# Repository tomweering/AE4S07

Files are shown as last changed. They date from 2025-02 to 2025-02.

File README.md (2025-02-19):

# AE4S07: Micropropulsion Individual Project 

## Project ID: 60d Parallelepiped Tank Design for CubeSat  
**Supervisor:** A. Cervone  
**Type:** Analysis + Design  

## Overview
Designing a parallelepiped-shaped tank for a green mono-propellant CubeSat system, using additive manufacturing techniques.

## Model Render

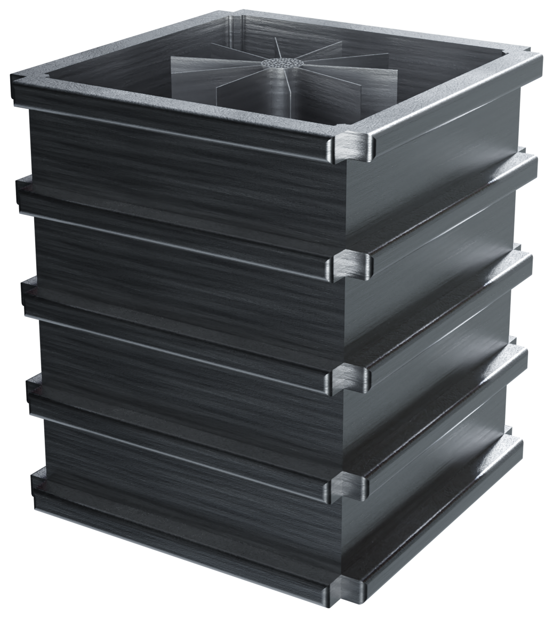
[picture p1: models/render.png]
Parallelepiped Tank Render


## Keywords
CubeSat, Propulsion, Parallelepiped Tank, Green Propellant, Additive Manufacturing

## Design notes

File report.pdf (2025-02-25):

AE4S07 Micropropulsion: Individual Project TU Delft
February 2025
Tom Weering

Tom Weering 5009057

## Report 60d Preliminary design of a parallelepiped-shaped tank for CubeSat green mono-propellant systems

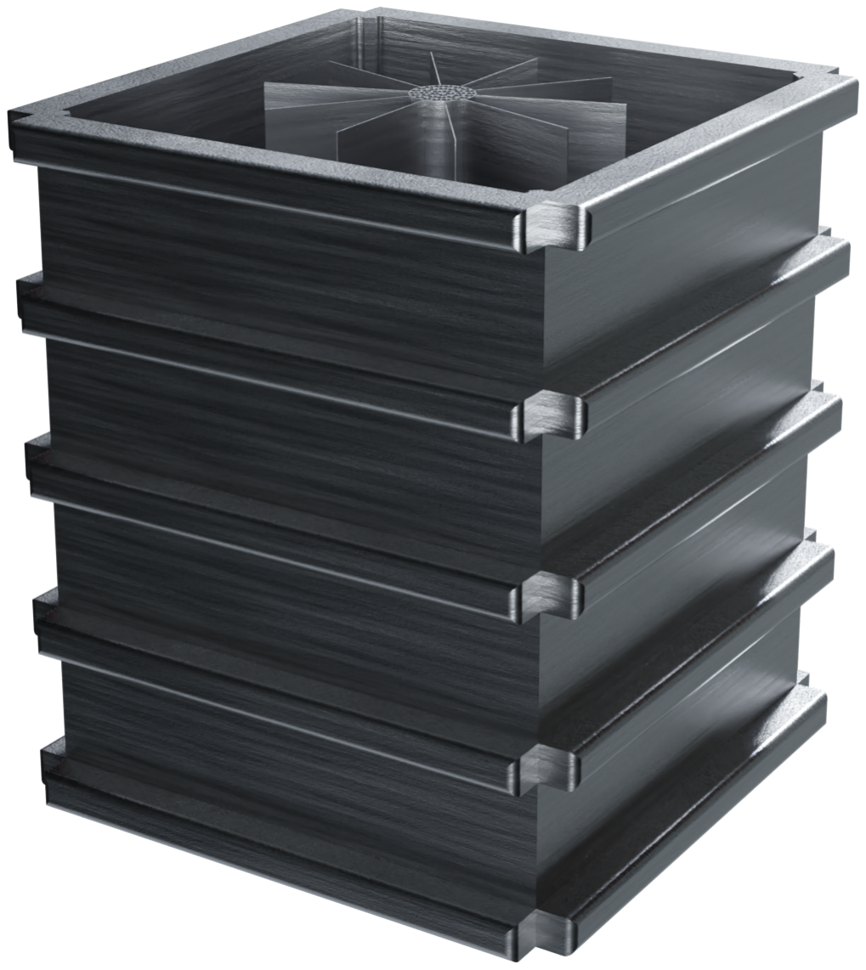
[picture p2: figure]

## Problem Formulation

As space miniaturization advances, it becomes increasingly important to integrate diverse fields of knowledge, such as green fuels, advanced manufacturing techniques, and innovative design shapes, to drive progress in the sector. This project focuses on the analysis and preliminary design of a CubeSat propellant tank with a parallelepiped shape, utilizing additive manufacturing (AM) techniques for green monopropellants. The goal is to design a competitive design solution, taking note of their respective advantages and disadvantages (Table 1).

Designing a parallelepiped-shaped propellant tank for CubeSats introduces both challenges and opportunities, especially when incorporating AM techniques and green monopropellants. The parallelepiped geometry offers space efficiency and modularity, which

Individual Project | Tom Weering

simplifies spacecraft integration. However by it’s nature it is not an ideal shape for a pressure vessel which will limit the internal pressure.

AM also presents multiple benefits for CubeSat propulsion systems, including rapid prototyping and simplyfing the manufacturing process. It also enables the creation of more complex geometries. AM also supports high-performance alloys, such as Ti-6Al-4V and Inconel [14], ensuring structural integrity and chemical compatibility with green monopropellants. Nevertheless, challenges remain, such as post-processing requirements for flight-grade standards, print orientation, thermal issues, the need for supports etc.

Green monopropellants offer improved safety, lower toxicity, reduced environmental impact, and competitive performance compared to traditional propellants. Additionally, they exhibit better storage stability. However, due to their relatively recent development and limited testing, it is important to consider their compatibility with the selected structural material, propulsion management systems, and other related components.

Advantages | Disadvantages
Parallelepiped-Shaped Tanks
Space Efficiency | Sharp corners
Modularity | Pressure limited
| Additive Manufacturing
Rapid Prototyping | Surface Finish
Complex Geometries | Chemical Compatibility
Green (Mono-)Propellant
Safety | Chemical Compatability
Storage Stability | Limited Knowledge

Table 1: Key Advantages and Disadvantages of Parallelepiped-Shaped Tanks, Additive Manufacturing, and Green Monopropellants.

The success of this project hinges on a comprehensive understanding of the interaction between these factors, with the goal of designing a propellant tank that aligns with our current knowledge of these interactions. The design will aim to provide a solution that is easily integrable into existing CubeSat formats (primarily 3U, as detailed later) and leverages the capabilities of current additive manufacturing (AM) techniques, ensuring compatibility with green monopropellants. In doing so this report aspires to answer the following two research questions:

RQ1: What is the most suitable design for a parallelepiped-shaped tank, to meet the identified constraints and requirements?

RQ2: What are the most suitable materials, dimensions and shape/fluidic interfaces which allow for a fully operational design of the tank?

## Requirements

Before exploring potential design options and developing a preliminary design, it is essential to first define the problem through a set of requirements. This was achieved through an internal literature review, including an analysis of the Lunar Flashlight mission [12], reference to design manuals for pressure vessels [4], and research into constraints associated with additive manufacturing [1] and the use of green monopropellants [15]. Following a systems engineering approach, top-level requirements were established and subsequently broken down into related sub-requirements, resulting in the requirements discovery tree illustrated in Figure 1.

The requirements highlighted in light green represent stakeholder requirements, derived directly from the project description. Below these are system-level requirements, followed by more specific requirements that pertain to "subsystems" of the tank being designed. These subsystems include structural aspects, propellant management devices, CubeSat design specifications, and constraints related to additive manufacturing.

Each requirement is assigned a unique ID in the format PAMGMT-STK-XX-SYS-SUB-XX, where SUB represents one of the four subsystems: STR (Structure), PMD (Propellant Management Device), CDS (CubeSat Design Specification), or AM (Additive Manufacturing). The acronym PAMGMT stands for Parallelepiped-shaped Additively Manufactured Green Monopropellant Tank. This structured approach ensures clear traceability, linking each requirement to higher-level system goals and demonstrating how individual requirements contribute to fulfilling broader, less strictly defined objectives. The complete overview listing every requirement along with the associate rationale for including them is given in the Table below (see Table 3).

An implicit requirement is that the selected material must be compatible with L-PBF or EB-PBF additive manufacturing processes and chemically resistant to green monopropellants. According to literature [14], several materials have been identified as suitable for these manufacturing techniques, with some also exhibiting favorable chemical compatibility with green monopropellants. Table 2 provides an overview of these materials. These options will serve as the foundation for material selection in the subsequent preliminary design phase. In the table, "A" indicates excellent chemical compatibility with the specified green monopropellant. Throughout this report, L-PBF will be used as the default method for additive manufacturing, as EB-PBF generally involves higher costs due to the requirement for a vacuum environment [7]. However, if thermal issues arise with L-PBF, EB-PBF may be considered as an alternative (except for SS304L).

Table 2: Material Compatibility with Green Propellants [14]

MATERIAL | HNP225 | LMP103S | AFM315E | FLP-106
Ti-6Al-4V | A | A | A | A
SS316L | A | A | A | A
SS304L | A | A | A | A
Inconel 625 | A | A | A | A

*Only compatible with L-PBF (Laser Powder Bed Fusion) process.

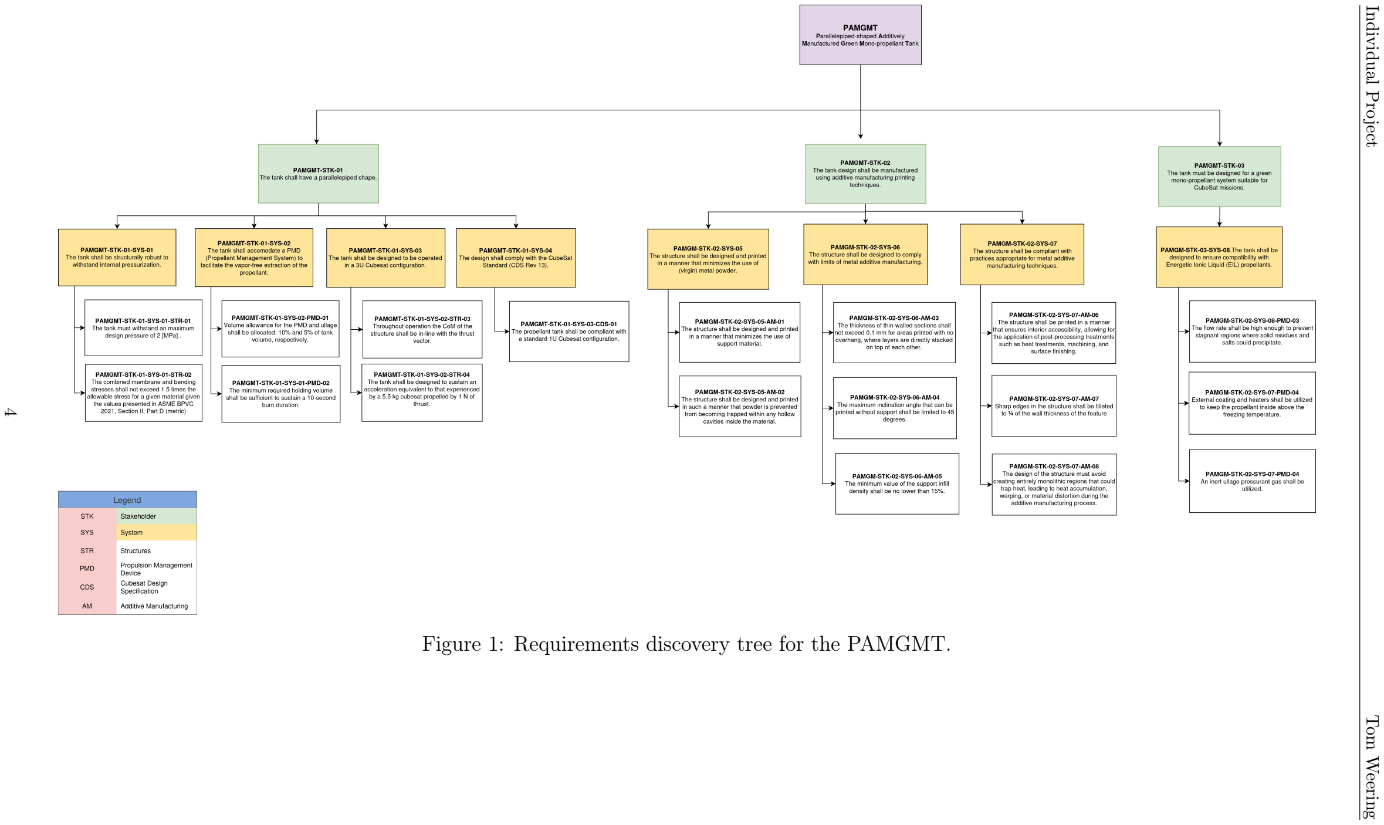
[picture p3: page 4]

Individual Project Tom Weering Figure 1: Requirements discovery tree for the PAMGMT.

4

Individual Project Tom Weering Requirement Index Description Rationale PAMGMT-STK-01 The tank shall have a parallelepiped shape. Defined by supervisor. PAMGMT-STK-01-SYS-01 The tank shall be structurally robust to withstand internal pressurization. Regardless of the PMD, engine type, or propellant used, some ullage pressure is necessary. Given the tank’s parallelepiped shape, special attention must be paid to ensuring structural integrity. PAMGMT-STK-01-SYS-01-STR-01 The tank must withstand an maximum design pressure of 2 [MPa]. monopropellant microthrusters produce 0.1–1 N of thrust [6], and for a specific 1 N thruster, chamber pressure ranges from 0.45 to 2.2 MPa [15]. To accommodate various thruster types, a Maximum Design Pressure (MDP) of approximately 2 MPa was chosen. PAMGMT-STK-01-SYS-01-STR-02 The combined membrane and bending stresses shall not exceed 1.5 times the allowable stress for a given material given the values presented in ASME BPVC 2021, Section II, Part D (metric) The sizing must go according to standardization practices appropriate for pressure vessels. The ASME (The American Society of Mechanical Engineers) sizing for infinite rectangular pressure vessels was adapted for this purpose. PAMGMT-STK-01-SYS-02 The tank shall accomodate a PMD (Propellant Management System) to facilitate the vapor-free extraction of the propellant. Without settling thrust maneuvers, vapor-free propellant flow cannot be ensured without a PMD. Over time, liquid and gas phases mix, potentially covering the outlet. This can lead to combustion instabilities or even engine failure. [11] PAMGMT-STK-01-SYS-02-PMD-01 Volume allowance for the PMD and ullage shall be allocated: 10% and 5% of tank volume, respectively. These values are used to provide a realistic estimate of the propellant volume while accounting for the space occupied by the PMD [15]. PAMGMT-STK-01-SYS-01-PMD-02 The minimum required holding volume shall be sufficient to sustain a 10-second burn duration. It is assumed a CubeSat burn typically lasts up to 10 seconds [6]. The PMD must supply enough propellant to sustain this duration, defining the minimum required holding volume. PAMGMT-STK-01-SYS-03 The tank shall be designed to be operated in a 3U Cubesat configuration Monopropellant thrusters are suitable for 3U and 12U CubeSats [6]. Since the market primarily targets 3U CubeSats, this propellant tank should be designed to align with that demand. PAMGMT-STK-01-SYS-02-STR-03 Throughout operation the CoM of the structure shall be in-line with the thrust vector. An asymmetrically designed PMD or an offset propellant mass will generate a moment proportional to the offset and thrust, requiring compensation from the attitude thrusters. PAMGMT-STK-01-SYS-02-STR-04 The tank shall be designed to sustain an acceleration equivalent to that experienced by a 5.5 kg Cubesat propelled by 1 N of thrust. A reference mass of approximately 5.5 kg was taken for a 3U CubeSat [22], which is expected to be accelerated by a 1 N thruster. This is considered suitable for a micropropulsion-driven CubeSat of this size and serves as a representative value for sizing the propellant tank. PAMGMT-STK-01-SYS-04 The design shall comply with the CubeSat Standard (CDS Rev 13). The CubeSat Design Specification (CDS) [21] is a widely recognized standard for CubeSat design. Complying with this standard ensures compatibility with other CubeSat components and systems. PAMGMT-STK-01-SYS-03-CDS-01 The propellant tank shall be compliant with a standard 1U Cubesat configuration. To create a versatile, "plug-and-play" system adaptable to various missions and configurations, the propellant tank dimensions were constrained to fit within a 1U CubeSat, ensuring adequate clearance for structural components like mounting points. PAMGMT-STK-02 The tank design shall be manufactured using additive manufacturing printing techniques. Defined by supervisor. PAMGM-STK-02-SYS-05 The structure shall be designed and printed in a manner that minimizes the use of (virgin) metal powder. Virgin metal powder will likely be required for flight parts [12], as studies suggest that reused powder can result in inconsistent material properties and performance. However, since this significantly increases costs, its use should be minimized. PAMGM-STK-02-SYS-05-AM-01 The structure shall be designed and printed in a manner that minimizes the use of support material. Since the supports will likely be made from the same virgin metal powder as the main structure, minimizing their use is essential to reduce material consumption. PAMGM-STK-02-SYS-05-AM-02 The structure shall be designed and printed in such a manner that powder is prevented from becoming trapped within any hollow cavities inside the material. Hollow structures without release holes trap powder, increasing mass and wasting material. PAMGM-STK-02-SYS-06 The structure shall be designed to comply with limits of metal additive manufacturing. Like any manufacturing method, additive manufacturing has unique constraints that must be considered during the design process. PAMGM-STK-02-SYS-06-AM-03 The thickness of thin-walled sections shall not exceed 0.1 mm for areas printed with no overhang, where layers are directly stacked on top of each other. A value of 0.1 mm is taken to be the minimum thickness that can be printed without support [23]. PAMGM-STK-02-SYS-06-AM-04 The maximum inclination angle that can be printed without support shall be limited to 45 degrees. A value of 45 degrees is taken to be the maximum angle that can be printed without support [23]. PAMGM-STK-02-SYS-06-AM-05 The minimum value of the support infill density shall be no lower than 15%. Support structures can be printed at a minimum distance of 2mm from eachother without causing thermal problems [23], a simple estimation on the available infill material for the supports can lead to a value as low as 5% but to remain conservative a value of 15% which is often utilized in conventional plastic 3D printing is used. PAMGM-STK-02-SYS-07 The structure shall be compliant with practices appropriate for metal additive manufacturing techniques. The design must align with metal additive manufacturing requirements to ensure successful fabrication, including post-processing considerations and proper handling after production. PAMGM-STK-02-SYS-07-AM-06 The structure shall be printed in a manner that ensures interior accessibility, allowing for the application of post-processing treatments such as heat treatments, machining, and surface finishing. Post-processing treatments are often necessary to improve the mechanical properties of the printed structure [12]. Ensuring interior accessibility is essential for applying these treatments effectively. PAMGM-STK-02-SYS-07-AM-07 Sharp edges in the structure shall be filleted to ¼ of the wall thickness of the feature. Sharp edges on exterior components, such as ribs, must be filleted to reduce stress concentrations and enhance safety by preventing injuries during post-production handling and assembly [13]. PAMGM-STK-02-SYS-07-AM-08 The design of the structure must avoid creating entirely monolithic regions that could trap heat, leading to heat accumulation, warping, or material distortion during the additive manufacturing process. Monolithic regions can trap heat, leading to thermal issues during the additive manufacturing process. To prevent these issues, the design must incorporate features that promote heat dissipation and prevent heat accumulation. PAMGMT-STK-03 The tank must be designed for a green mono-propellant system suitable for CubeSat missions. Defined by supervisor. PAMGM-STK-03-SYS-08. The tank shall be designed to ensure compatibility with Energetic Ionic Liquid (EIL) propellants. Energetic Ionic Liquid (EIL) propellants are a type of green monopropellant that offers high performance and low toxicity. The tank must be designed to accommodate the unique properties of EIL propellants to ensure safe and efficient storage and delivery. PAMGM-STK-02-SYS-08-PMD-03 The flow rate shall be high enough to prevent stagnant regions where solid residues and salts could precipitate. A notable issue with certain EIL propellants, particularly when used in propulsion systems, is the potential for slow decomposition. This can lead to the formation of solid residues and salt precipitation, which could create operational challenges, such as clogging of valves and feed lines. To prevent this, the propellant tank must be designed to ensure adequate flow rates (value of around 30mL/min taken from [15]) that prevent stagnation and promote propellant circulation. PAMGM-STK-02-SYS-07-PMD-04 External coating and heaters shall be utilized to keep the propellant inside above the freezing temperature. Energetic Ionic Liquid (EIL) propellants have a low freezing point, which can lead to solidification and clogging of the propellant lines. To prevent this, the tank must be equipped with external heating elements and coatings to maintain the propellant temperature above its freezing point.

PAMGM-STK-02-SYS-07-PMD-04 | An inert ullage pressurant gas shall be utilized. | To maintain the propellant in a liquid state, an inert ullage pressurant gas must be used.
Table 3: Requirements table

5

## Design Options

To effectively define the scope of the design problem, it is essential to systematically present all possible design options within the established constraints—namely, additive manufacturing, the use of green monopropellants, and a parallelepiped-shaped configuration. This ideation process is structured through a design option tree, which aims to comprehensively explore all conceivable alternatives at this stage within the defined design space.

As a baseline, the tank design used in the Lunar Flashlight mission [12] was considered, along with hypothetical design concepts such as those proposed by Shcheglov et al. [16] and various types of additively manufactured pressure vessels discussed in Tepponen et al. [20]. Based on this, several design possibilities were identified, including a generic parallelepiped-shaped configuration (rectangular but not necessarily conforming to the CubeSat standard and potentially incorporating angled surfaces), a rounded rectangular design, a variable thickness structure, an inner lattice design, a uniform thickness rectangular design, and an externally ribbed rectangular design.

These designs come with their own benefits and drawbacks [20]:

- Generic Parallelepiped Design

– Description: A generic rectangular tank design (i.e. follows from V “ |⃗a¨ p⃗bˆ ⃗cq|) that can be adapted to various enclosures but lacks predefined constraints.

– Advantages:
∗ Can be tailored for specific enclosures.

– Disadvantages:
∗ Hard to design due to fewer constraints.
∗ Cannot be designed as a "plug-and-play" solution.
- Rounded Rectangular Design

– Description: A rectangular tank with rounded edges to minimize stress concentrations and improve structural durability.

– Advantages:
∗ Reduces stress concentrations at corners, improving fatigue life.
∗ May marginally improve weight reduction in comparison to uniform thickness.

– Disadvantages:
∗ May slightly reduce usable internal volume due to rounded edges.
- Variable Thickness Rectangular Design

– Description: A rectangular tank with varying wall thickness to optimize weight-to-strength ratio.

– Advantages:
∗ Improves weight-to-strength ratio by reinforcing high-stress areas.

∗ Reduces material usage, leading to cost savings.
∗ Enhances fatigue life by minimizing stress concentration zones.

– Disadvantages:
∗ Complex manufacturing due to varying wall thickness.
∗ Requires advanced simulation and optimization tools.
∗ Potential issues with residual stresses and distortions during printing.
- Uniform Thickness Rectangular Design

– Description: A simple rectangular tank with uniform wall thickness for ease of manufacturing and predictable performance.

– Advantages:
∗ Simplifies manufacturing and analysis with minimal support structures. ∗ Predictable mechanical behavior under pressure loads (well understood from theory [4]).
∗ Easier post-processing and quality control.

– Disadvantages:
∗ Not optimized for weight reduction.
∗ Doesn’t fully leverage the potential of additive manufacturing.
- Inner Lattice Rectangular Design

– Description: A rectangular tank with an internal lattice structure to reduce weight while maintaining structural integrity.

– Advantages:
∗ Enables significant weight reduction while maintaining structural integrity. ∗ Difficult to manufacture using traditional methods, making AM a perfect fit.

– Disadvantages:
∗ Can introduce stress concentration points at lattice junctions.
∗ Post-processing and inspection are more complex.
∗ Inner ribs require filleting or other design modifications to prevent propellant entrapment.
- Ribbed Rectangular Design

– Description: A rectangular tank reinforced with external or internal ribs to improve stiffness and resistance to buckling.

– Advantages:
∗ Increases stiffness and resistance to buckling.
∗ Provides significant weight reduction while maintaining structural integrity. ∗ Ribs can serve as mounting points for structural integration.

– Disadvantages:
∗ Requires additional supports between ribs during manufacturing.

These design options were evaluated using a trade-off matrix, considering factors such as weight reduction, design simplicity, adaptability, volume utilization, and printability. As shown in Table 4, the ribbed and uniform rectangular designs emerged as the most favorable. While they may not be the most intricate or most compelling options for showcasing additive manufacturing techniques, they offer a balanced combination of simplicity, high printability, and well-documented stress and thickness relationships [3] [4]. Therefore given the objectives of this design and analysis study these options were chosen to be implemented in the preliminary sizing.

Design | Weight Reduc- tion (5)

Design
Simplicity
(4)

Adaptable
(3)

Volume
Utilization (2)

Printable
(1)

Total
Score
Generic Parallelepiped | 2 (10) | 1 (4) | 5 (15) | 5 (10) | 2 (2) | 41
Rounded Rectangular | 3 (15) | 3 (12) | 3 (9) | 3 (6) | 4 (4) | 46
Variable Thickness | 4 (20) | 2 (8) | 3 (9) | 3 (6) | 1 (1) | 44
Uniform Thickness | 2 (10) | 5 (20) | 4 (12) | 4 (8) | 5 (5) | 55
Inner Lattice | 4 (20) | 2 (8) | 3 (9) | 2 (4) | 4 (4) | 45
Ribbed Rectangular | 4 (20) | 4 (16) | 4 (12) | 4 (8) | 4 (4) | 60

Table 4: Trade-off analysis of different tank designs. Numbers in parentheses represent weighted scores.

The next set of design considerations involves selecting the most appropriate Propellant Management Device (PMD). Given PAMGMT-STK-01-SYS-02, which aims to ensure vapor-free propellant delivery to the engine, a thorough evaluation of PMD options is essential. The choice of PMD directly affects the required internal pressure, influencing skin thickness and other structural aspects of the design. The most commonly used PMDs in CubeSats include elastic diaphragms, actuated expulsion mechanisms, surface tension components, and gas pressurization [14].
These common PMD types are described and their advantages and disadvantages are presented bellow [11]:
- Elastic Diaphragms

– Description: Utilizes a flexible membrane that separates the pressurant gas from the liquid propellant.

– Advantages:

∗ Prevents gas-propellant mixing, ensuring vapor-free propellant delivery. ∗ Effective for slosh control.

– Disadvantages:

∗ Limited lifespan due to elastomeric material degradation. ∗ Additional mass due to the diaphragm.

- Actuated Expulsion Mechanisms (Pistons, Bladders etc.)

– Description: Uses some type of actuated mechanism such as pistons, bladders or even pumps to actively expel propellant.

– Advantages:

∗ The ability to control the propellant mass flow rate.
∗ High expulsion efficiency.
∗ Allows for higher propellant storage volumes by eliminating the need for gas pressurization systems (in case of using pumps).

– Disadvantages:

∗ Requires power.
∗ Increased system mass and complexity.
- Surface Tension Components (Capillary PMDs)

– Description: Utilizes capillary forces to control and direct liquid propellant within the tank, ensuring vapor-free expulsion under microgravity conditions.

– Advantages:

∗ Passive operation with no moving parts, increasing reliability.
∗ Lightweight and highly adaptable to different tank geometries.
∗ Effective in managing liquid positioning and preventing vapor ingestion.

– Disadvantages:

∗ Performance depends on precise geometric design and wettability properties.
∗ Limited capability to handle high flow rates compared to active expulsion methods.
∗ Complex manufacturing and integration, especially for intricate structures.
- Gas Pressurization

– Description: Uses inert gas (e.g., helium, nitrogen) to directly pressurize the propellant.

– Advantages:

∗ Simple design, widely used in propulsion systems.

– Disadvantages:

∗ Requires large storage tanks for pressurant gases. ∗ Creates larger internal pressure.

A trade-off matrix was created based on the criteria of weight reduction, design simplicity, adaptability, ullage pressure, and power consumption. The last two criteria specifically assess the additional internal pressure required by each PMD and whether the system requires power to operate (with a score of 5 indicating no power requirement and 1 representing a high, continuous power demand). The results are presented in Table 5. Surface tension methods are clearly favored due to their simplicity, lack of power requirements, and minimal impact on the necessary ullage pressure.

PMD Type | Weight Reduc- tion (5)

Design
Simplicity (4)

Adaptable
(3)

Ullage
Pressure (2)

Power
Consumption (1)

Total
Score
Elastic Diaphragms | 2 (10) | 3 (12) | 3 (9) | 2 (4) | 3 (3) | 38
Actuated Expulsion | 3 (15) | 2 (8) | 5 (15) | 4 (8) | 1 (1) | 47
Surface Tension | 5 (25) | 5 (20) | 2 (6) | 4 (8) | 5 (5) | 64
Gas Pressurization | 4 (20) | 4 (16) | 3 (9) | 1 (2) | 2 (2) | 49

Table 5: Trade-off analysis of different PMD options. Numbers in parentheses represent weighted scores.

After selecting for the PMD category, various components within the surface tension category can still be considered to ensure vapor-free propellant delivery. Table 6 provides an overview of these components, including a brief description, their advantages, and their disadvantages.

According to literature [6], monopropellant thrusters are among the most suitable propulsion choices for 3U and 12U CubeSats, with the current market primarily catering to the 3U class. The proposed tank should be compact enough to fit within the structural frame of a 1U CubeSat while being designed primarily for integration into 3U CubeSat missions. This means it must withstand the accelerations typical for such a class of spacecraft.

As a baseline, an acceleration of approximately 0.018 [g] is assumed, based on a 5.5 [kg] spacecraft mass [22] and a total thrust of about 1 [N] (see PAMGMT-STK-01-SYS-02-STR-04). Unlike the Lunar Flashlight mission, this tank is not being developed for a specific mission but rather as a versatile, multi-functional, plug-and-play solution. For most CubeSats, propulsion is primarily required for orbit adjustments and station-keeping maneuvers, typically involving burn durations of no more than 10 seconds (see PAMGMT-STK-01-SYS-01-PMD-02).

Given these constraints, the CubeSat is expected to experience low accelerations for relatively short periods. From Table 6, sponges and vanes emerge as suitable options for guiding and controlling propellant flow, with porous elements inherently incorporated within sponge structures. While baffles could help mitigate sloshing, their necessity is reduced due to the relatively small propellant mass fraction in a 3U CubeSat and the expected low acceleration levels. Therefore, at this stage of the design, sloshing is not considered a critical concern. Figure 2 shows the completed design option tree with all previously discussed options.

Name | Image | Description | Advantages | Disadvantages
Vane | | Lightweight "sheet metal" structures that use surface tension to guide propellant to the outlet. Propellant clings to the vanes and moves along formed corners. | Simple, low cost, effec-tive for low-acceleration burns, reliable. | Cannot lift propellant at high accelerations, lim-ited to low-g applica-tions.
Gallery | | Closed flow paths covered with porous elements to prevent gas ingestion while allowing liquid flow. Used for vapor-free pro-pellant delivery. | Effective at high accel-erations, ensures gas-free flow, reliable for long-duration missions. | Heavy, complex, ineffi-cient, lower reliability.
Sponge | | Open metal structures with ta-pered gaps that control propel-lant flow and prevent gas in-trusion. Used in stationkeep-ing and settling applications. | Refillable after accelera-tion, reliable, effective in low-g conditions. | Cannot retain liquid at high accelerations, lim-ited liquid retention ca-pacity.
Trap | | Solid wall containers hold-ing propellant with porous element-covered inlets, used for one-time critical burns. | Suitable for high-acceleration events, effective for gas reten-tion. | Not passively refillable in zero-g, unsuitable for fre-quent maneuvers.
Trough | | Uses hydrostatics to retain propellant in an acceleration field. Can be designed for refillability or omnidirectional retention. | Works in high-g con-ditions, useful for spe-cific launch and reentry needs. | Heavy, expensive, not mass-efficient compared to sponges.
Porous Ele-ments | | Used in various PMDs to al-low liquid flow while prevent-ing gas penetration. Com-monly made from woven screen or perforated sheet. | Ensures gas-free propel-lant delivery, essential for PMD performance. | Small pores increase flow resistance, difficult to manufacture and inte-grate.
Baffle | | Structures used to reduce sloshing by limiting propellant movement within the tank. | Enhances stability, pre-vents unwanted fluid mo-tion. | Does not assist in di-rect propellant retention, adds weight.

Table 6: Comparison of various Propellant Management Devices (PMDs). [19]

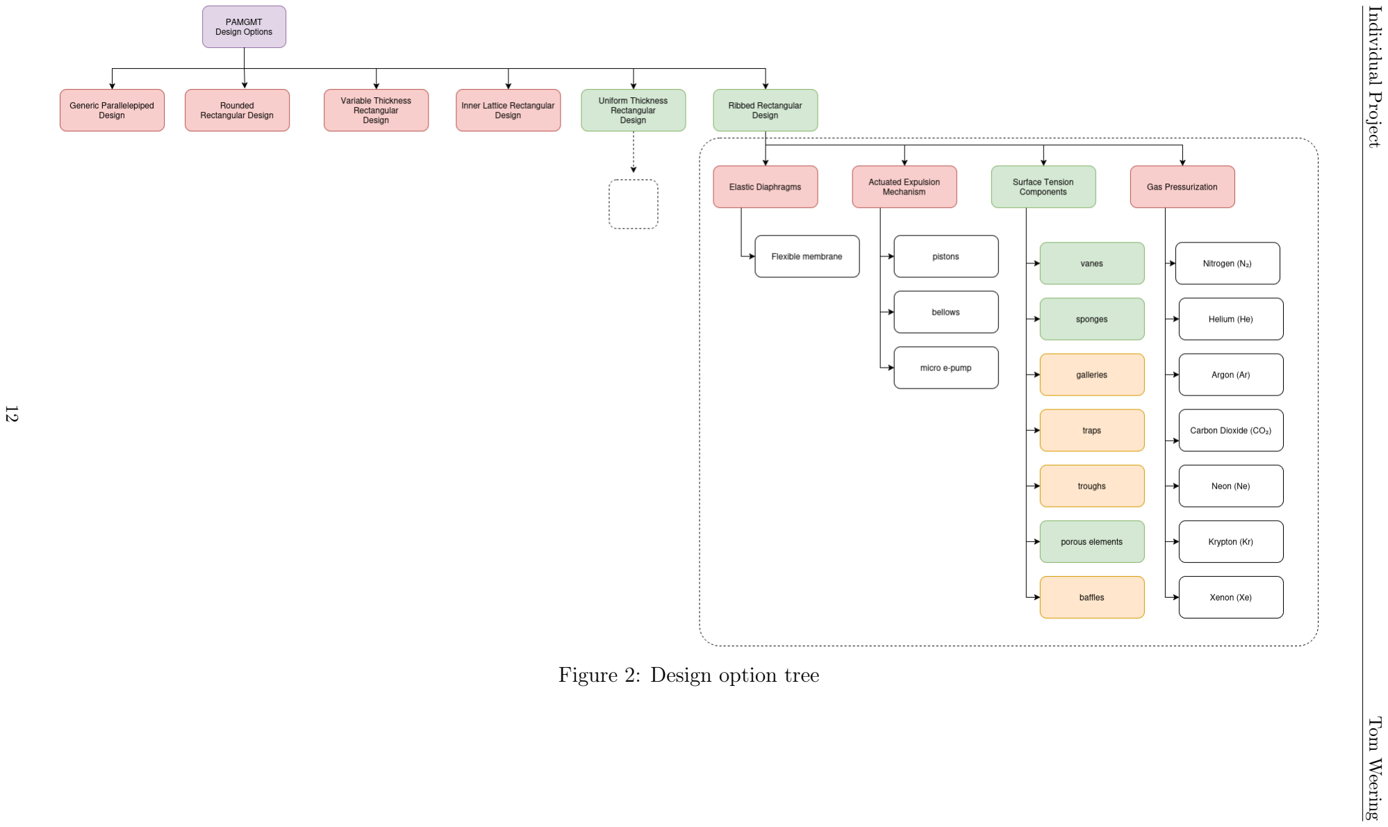
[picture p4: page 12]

Individual Project Tom Weering Figure 2: Design option tree

12

## Preliminary Design

Main Structure

After specifying the design options for the tank dimensions and the PMD system, and defining the requirements, it is necessary to discuss the method used for sizing the tank. To design both a uniform thickness and ribbed rectangular pressure vessel, a method from the American Society of Mechanical Engineers (ASME) was utilized to relate the internal pressure to the required thickness and the number or spacing of ribs (i.e., stiffening elements). This method idealizes a cross-section of an infinitely long rectangular pressure vessel. Alternative methods for finite pressure vessels are described by Blach et al. [4].

The decision not to use these alternative methods (e.g., the small and large deflection methods mentioned by Blach et al.) was due to the stiffening effect induced by the corners of a 3D finite pressure vessel, which may eleviate the internal stress. To remain conservative and consistent with established standards, the ASME code method [3] was chosen. Additionally, using the ASME code offers the advantage of readily available resources and example calculations, as demonstrated by Blach et al. (calctoys). (https://github.com/thepvguy/calctoys/tree/master) Further mass reductions could be made in the future by employing less conservative sizing methods and performing real-life pressurization validation tests. Given the chosen design options the following two generalized cross-sections were used as shown in Figure 3a and Figure 3b

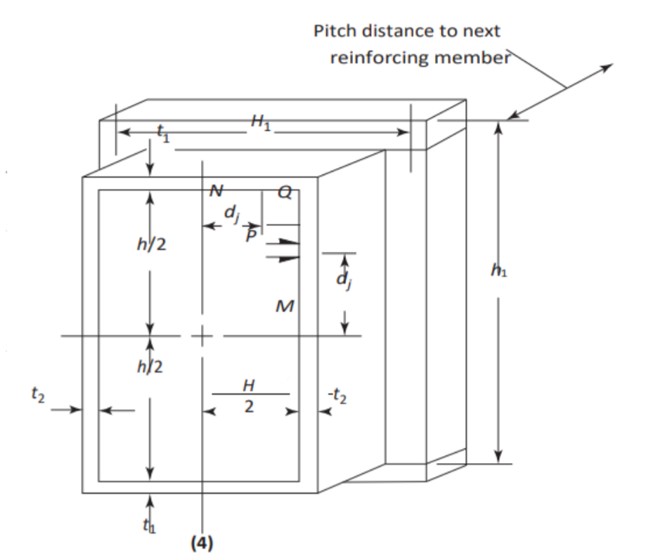
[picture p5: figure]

(a) Cross-section of unstiffened rectangular pressure vessel.

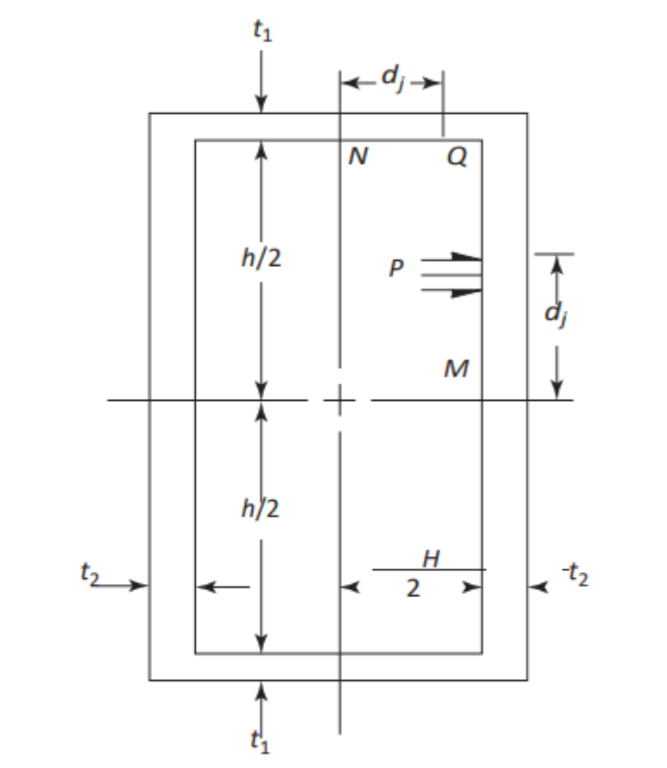
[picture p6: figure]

(b) Cross-section of stiffened rectangular pressure vessel

Figure 3: Parametric rectangular presssure vessel cross-sections from ASME handbook [3]

As required by PAMGMT-STK-01-SYS-01-STR-02, the combined membrane and bending stresses shall not exceed 1.5 times the allowable stress for a given material, as specified in ASME BPVC 2021, Section II, Part D (metric) [2]. The allowable stress varies with temperature, and a simplified radiative heat balance is implemented within the code (see section ) to provide a conservative estimate of the allowable stress.

The script in the code section utilizes the method outlined in Appendix 13 of the ASME handbook [3] to evaluate compliance with the specified requirement. The dimensions of the rectangular pressure vessel are predefined to fit within a 1U enclosure, as stipulated by PAMGMT-STK-01-SYS-03-CDS-01, ensuring sufficient clearance for surrounding structures (Table 8). The ribbed or stiffened configuration, illustrated in Figure 3a, is designed using predefined stiffener properties listed in Table 7.

Table 7: Summary of stiffener properties

Parameter | Description | Value
ts hs | Thickness Height of stiffener | 5 mm 5 mm

Table 8: Summary of Rectangular Pressure Vessel Dimensions

Parameter | Description | Value
h L | Side length Height | 70 mm 90 mm

The spacing between stiffeners is calculated using the following equation:

P “

L ´ hs
n ´ 1

(1)

where:

- P = Spacing between stiffeners
- L = Total height of the tank
- hs = Height of each stiffener
- n = Number of stiffeners

Based on the material selected, as shown in Table 2, the adapted method was applied with the assumption that t1 “ t2 (i.e., a uniform thickness cross-section). As illustrated in Figure 4, the safe pressure ranges are influenced by factors such as internal pressure, material properties, and the presence of stiffening elements. The results demonstrate that the stiffened structure allows for thinner walls at any given pressure, with Ti6Al4V, in particular, performing exceptionally well.

Naturally, the stiffened structure will require additional mass, and the choice of materials is also influenced by their density and the cost of the metal powder needed for construction. This relationship is illustrated in Figure 5, where the radial distance from the origin represents the viability of each design based on these two factors. The top 5 closes points to the origin are tabulated in Table 9.

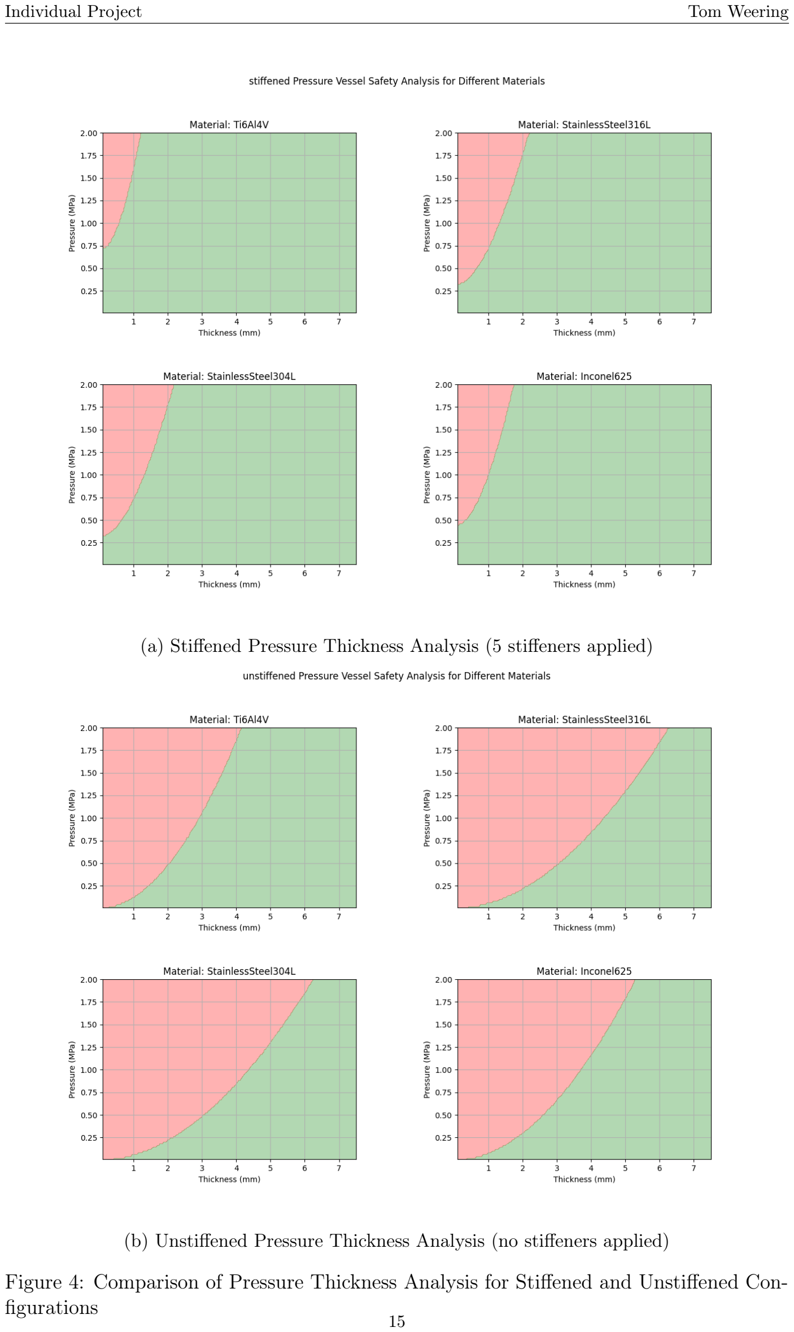
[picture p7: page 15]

(a) Stiffened Pressure Thickness Analysis (5 stiffeners applied)
(b) Unstiffened Pressure Thickness Analysis (no stiffeners applied)

Figure 4: Comparison of Pressure Thickness Analysis for Stiffened and Unstiffened Configurations

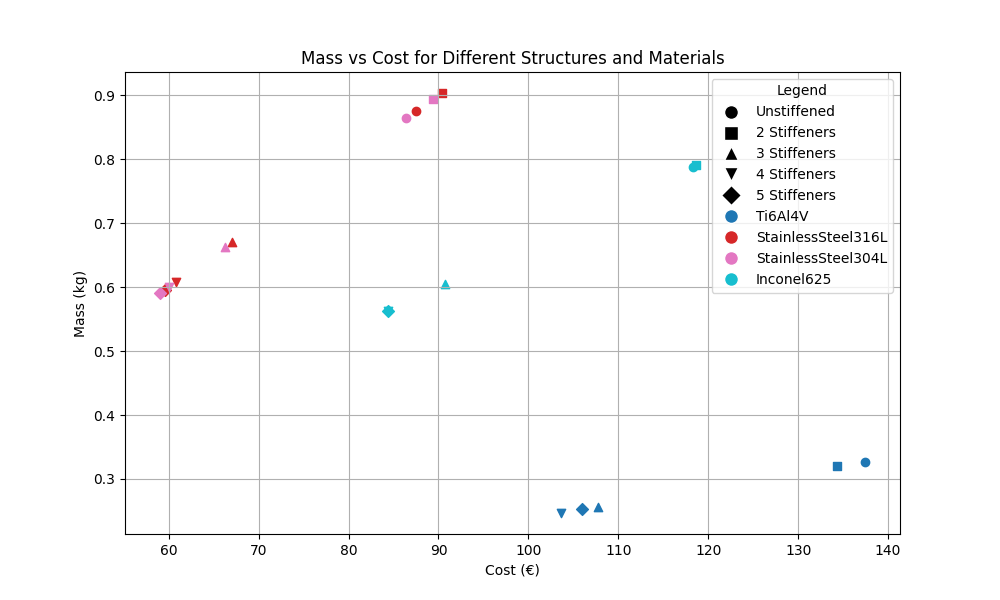
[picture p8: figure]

Figure 5: Mass / Cost Tradeoff for given structure type and material at a MDP of 2 [MPa]

Table 9: Top 5 Closest Points to the Origin (Mass and Cost)

Material | Structure | Mass (kg) | Cost (€) | Thickness (mm)
SS304L SS316L SS304L SS316L SS304L | 5 Stiffeners 5 Stiffeners 4 Stiffeners 4 Stiffeners 3 Stiffeners | 0.59 0.60 0.60 0.61 0.66 | 59.06 59.58 60.08 60.83 66.27 | 2.13 2.13 2.59 2.61 3.42

As per requirement PAMGMT-STK-01-SYS-01-STR-01, the tank is sized for a internal pressure of 2 [MPa] which will be maintained through an inert pressurant as per requirement PAMGM-STK-02-SYS-07-PMD-04. From looking at the graphs at a pressure of 2 [MPa]. It is clear that although the Titanium options are extremely lightweight, they come with the highest costs. On the other hand, the stainless steel options are the most affordable but typically have the greatest mass. The top 5 entries in the table above represent the best solutions if cost and mass were equally prioritized. However, other factors like PMD sizing, propellant requirements, and necessary supports must also be considered in the trade-off analysis. Therefore, further investigation into these aspects is necessary.

Vane sizing

As demonstrated in the previous sections, the design must include a method for extracting vapor-free propellant to meet the requirement PAMGMT-STK-01-SYS-02. Surface tension devices were selected as the most suitable solution given the constraints, with sponges and vanes being the preferred options. The vanes will be positioned at the corner

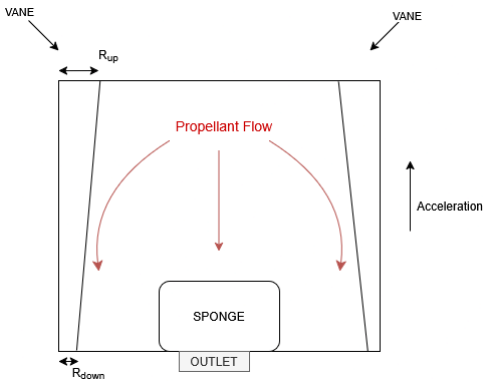
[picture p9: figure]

Figure 6: Diagram of PMD showing propellant flow.

points to prevent fluid from becoming trapped and to direct the propellant downward. Additionally, a central sponge will be incorporated to retain a specific amount of propellant, which will then be connected to the outlet. This has been illustrated in Figure 6.

The sizing of the vane was determined using established literature [8] [19] and is based on the following pressure balance: propellant will flow along the vane only if the "downstream radius" is sufficiently small. Essentially, the surface driving pressure is counteracted by dynamic forces, viscous losses, and hydrostatic forces. If the driving pressure is not strong enough to overcome these opposing forces, the propellant will not flow. This force balance can be represented by the following equation:

σ

ˆ
1

Rdown

´

1

Rup˙
“ ρpzdown ´ zupq ` 2µQs²L
A³

`

ρQ²
2A²

(2)

Where:

- σ - Surface tension of the propellant
- Rdown - Downstream radius of curvature
- Rup - Upstream radius of curvature
- ρ - Density of the propellant
- zdown - Vertical position at the downstream point
- zup - Vertical position at the upstream point
- µ - Dynamic viscosity of the propellant
- Q - Volumetric flow rate of the propellant
- s - Wetting area of the vane.
- L - Length of the flow path along the vane
- A - Vane surface area.

The first term on the right-hand side represents the hydrostatic losses, the second term accounts for the viscous losses, and the third term corresponds to the dynamic pressure losses. Several assumptions and simplifications are made: first, the hydrostatic losses are neglected because the acceleration vector is largely aligned with the flow vector. Additionally, it is assumed that the wetting area is equal to the total surface area of the vane. This assumption is made because the wettability of the propellants is not fully understood and would require additional effort to model accurately. Given the limited time available, it is assumed that complete wetting will result in the maximum viscous losses.

Due to the unknown liquid properties of the propellants, such as viscosity and surface tension, similar liquids were used as references. For AF-M315E, an ethylene glycol/glycerin mixture was used; for LMP-103S, ethanol-water mixtures served as a reference; nitromethane was used for HNP225; and a nitromethane/acetonitrile mixture was used for FLP-106 [17], [5],[10]. Extra care was also taken that the overhang angle created between Rup and Rdown could not surpass 45˝ as per requirement PAMGM-STK-02-SYS-06-AM-04.

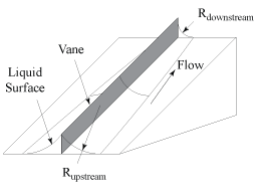
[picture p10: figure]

Figure 7: Vane sketch

Based on these assumptions and a constant flow rate of 30 mL/min (as per PAMGM-STK-02-SYS-08-PMD-03) regardless of the propellant type, the dynamic and viscous losses were minimal, with only a minimal difference in up-/downstream vane radius. As a result, a relatively small vane was selected using the dimensions shown in Table 10.

Table 10: Summary of Vane Radius Dimensions

Parameter | Description | Value
Rdown Rup | Vane radius (downstream) Vane radius (upstream) | 0.75 mm 0.84 mm

Additionally a spacing of around 1.5 [mm] was utilized to give enough clearance between the two vane halves and to ensure printability.

Sponge sizing

Additionally, a certain volume of propellant must be retained within a sponge. By positioning sponge panels (thin solid sheets) close together, liquid can be contained in the gaps, allowing large quantities of propellant to be managed even during thruster accelerations. At sufficiently high lateral accelerations, the propellant does not need to remain continuous and may exist in two separate regions of the sponge. This could result in isolated, inaccessible propellant within the sponge. [19]

alimit “

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
- alimit = limiting acceleration

•

dg
dz = gradient of gap size with respect to height
- σ = absolute surface tension
- ρ = liquid density
- g = gap size

It should be noted that the acceleration vector is assumed to align with the core of the sponge, around which the plates radiate outward (see Figure 6). This alignment suggests that the acceleration is unlikely to impose any significant constraints on the sponge’s design. The sponge is sized to hold enough propellant for a 10-second burn, as specified by requirement PAMGMT-STK-01-SYS-01-PMD-02. The inner core will provide the necessary supply, while the surrounding radial plates are sized to ensure adequate taper, minimizing the likelihood of flow separation under perpendicular acceleration (should that occur during re-orientation of the spacecraft) [9].

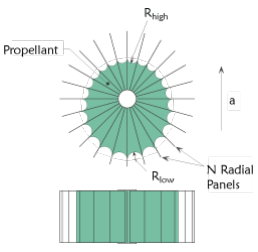
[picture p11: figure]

Figure 8: Sponge sketch

The thickness of the radial plates is constrained by requirement PAMGMT-STK-01-SYS-02-PMD-01. Running the main script, as shown in the code section , reveals that, based on the flow and burn time requirements, the sponges must extend up to the ceiling of the tank. It became apparent that the core would need to be quite large, and the thickness of the radial plates would be less than 1 mm. Previous work in additively manufacturing PMDs [18] highlighted the importance of aspect ratio (i.e., the height-to-thickness ratio of the radial plates) for successful printing. Without a central core to provide rigidity, the print would likely fail based on the current results. Therefore, it is crucial that the core is made of a porous material that also connects to the radial plates. This becomes even more critical since the core is too large to depend on surface tension or capillary action to prevent gas injection. A centrally located porous material helps block gas bubbles, with the bubble point pressure (∆P) being key to the performance of the porous device. This pressure defines the minimum level required to prevent gas from passing through the barrier (see Equation (4)).

∆PBP “

2σ cospαq
r

(4)

- PBP = bubble point pressure
- σ = absolute surface tension
- α = contact angle
- r = pore radius

A bubble point pressure of 200 [Pa] is selected as a baseline, based on a H2O2 propellant system [18]. It is likely that the propellants used in this design would require a higher bubble point pressure due to their increased viscosity and surface tension compared to H2O2. However, increasing this pressure would necessitate a reduction in the pore radius, which would complicate the printing process of the sponge. The sponge, especially the central porous core, represents the most challenging aspect in terms of printability, making it the most difficult component to manufacture in bringing the proposed designs to reality. The feasibility of printing the porous central core with a lattice structure, based on the calculated pore radius, should be verified through a series of test prints.

Supports

In accordance with the requirement PAMGM-STK-02-SYS-05-AM-01, support material should be minimized. For the proposed structures with stiffeners, supports are necessary due to the 90-degree overhang of these elements. However, printing solid rectangular blocks from the chosen metallic powder would be inefficient. To address this, an effort was made to design a more material-efficient support structure. A 15% infill was selected in line with PAMGM-STK-02-SYS-06-AM-05. The choice of infill pattern is particularly important, as PAMGM-STK-02-SYS-05-AM-02 specifies that powder should not become trapped, nor should the pattern require excessive powder or cause any thermal problems, while still providing sufficient rigidity. Similar to sponge structures, it will be essential to validate different infill patterns through real-world test prints, with options like Gyroid infill being considered for its strength in all directions and its ability to avoid trapping powder in enclosed areas.

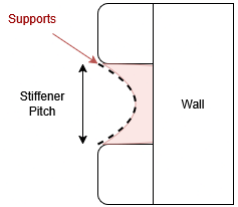
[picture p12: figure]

Figure 9: Sketch showing support curve in between two stiffeners

As per requirement PAMGM-STK-02-SYS-06-AM-04, overhangs of up to 45˝
can be
printed without the need for supports. An investigation was conducted to explore the possibility of incorporating a parabolic curve within the stiffener pitch (see Figure 9). With the intention that this could reduce the amount of material needed for the supports. A simple parabolic curve was designed to fit within the available space, ensuring it extended up to the thickness of the stiffeners without exceeding a 45˝ angle. (Through tanpθq “ dy{dx) Additionally, the "throat" of the curve was limited to 0.5 [mm] to maintain both proper printability and structural rigidity.

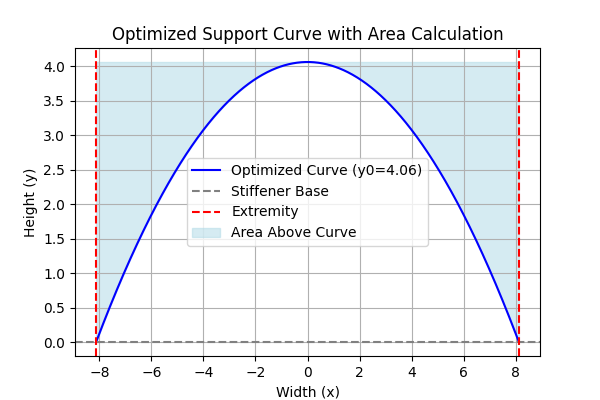
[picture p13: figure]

Figure 10: Optimized parabolic support curve for a 5 stiffener pitch.

In Figure 10, the optimized curve for 5 stiffener configuration is shown, the area above is calculated to be considered for the amount of support material required. Given the current proposed designs only the stiffeners necessitate these supporting structures. It is known from the literature that a theoretical overhang angle of 65˝
is could be feasible, suggesting that such a parabolic support structure might work. However, real-world validation tests would need to be performed to confirm this theory [23].

Trade Off

To conclude the design part of this report, the final design will be selected through a trade-off to identify the most suitable design option by evaluating different structure types, materials, and propellant types against several criteria, including the following:

- Mass: Lower mass is naturally preferred.
- Effective Tank Volume: A higher volume is desired for increased propellant capacity.
- Cost: Minimization of cost is preferred.
- Printability: This metric combines three sub-criteria:

– Higher rlattice (mm) to mitigate the issues with priting the porous central sponge material.
– Higher tsponge (mm) for better rigidity.

– Lower support mass for reduced material usage.

The min-max scaling approach is used to normalize the criteria between 0 and 1. In cases where minimization is desired (e.g., mass, cost, support mass), values are inverted after normalization:

Normalized Value “

1 ´

v´minpvq
maxpvq´minpvq

, if minimizing

v´minpvq
maxpvq´minpvq

, if maximizing

This ensures consistency in the interpretation of normalized values, where higher values are always better. The trade-off score is calculated as a weighted sum of normalized values. The chosen weights reflect the relative importance of each criterion:

- Mass: w “ 4 – Highly prioritized given it’s usual importance in space applications.
- Effective Tank Volume: w “ 1 – Given little weight since having a rectangular tank should already allow for higher volume utilization.
- Cost: w “ 3 – Given some more weight given the design should utilimately be able to compete with commercial offerings.
- Printability: w “ 2 – Also given some weight considering just prioritizing weight would cause many dimensions to be very close to the printable limit.

The trade-off score is calculated as follows:

Trade-off Score “

ř
wi

¨ Normalized Valuei
ř
wi
The results of this trade-off analysis are shown in Table 12, which presents the top 10 highest-rated designs out of a total of 80 variations. In contrast to the earlier mass and cost distribution, Titanium designs dominate the top 10 despite receiving low cost scores. This outcome highlights that, even with cost weighted at 3, Titanium remains the most favorable choice due to its superior performance across the other criteria.

Rank | Material | Structure | Propellant | Mass | Vol. | Cost | Print. | Score
1 2 3 4 5 6 7 8 9 10 | Ti6Al4V Ti6Al4V Ti6Al4V Ti6Al4V Ti6Al4V Ti6Al4V Ti6Al4V Ti6Al4V SS304L SS316L | 5 Stiffeners 4 Stiffeners 3 Stiffeners 5 Stiffeners 5 Stiffeners 4 Stiffeners 5 Stiffeners 4 Stiffeners 5 Stiffeners 5 Stiffeners | AF-M315E AF-M315E AF-M315E FLP-106 LMP-103S FLP-106 HNP225 LMP-103S AF-M315E AF-M315E | 0.986 1.000 0.996 0.986 0.986 1.000 0.986 1.000 0.339 0.328 | 1.000 0.929 0.816 1.000 1.000 0.929 1.000 0.929 0.786 0.786 | 0.174 0.191 0.176 0.174 0.174 0.191 0.174 0.191 1.000 0.993 | 1.000 0.919 0.867 0.735 0.705 0.648 0.642 0.621 0.790 0.788 | 0.747 0.734 0.706 0.694 0.687 0.680 0.675 0.674 0.672 0.665

Table 11: Top 10 designs with normalized values for different materials, structure types, and propellants.

The final design proposed based on the trade-off analysis is presented in Table 12. Titanium was chosen for its excellent mechanical properties, while AF-M315E was selected for its high surface tension, which enhances capillary action and enables effective liquid control in microgravity. Additionally, AF-M315E’s high maturity level for space applications adds to its suitability for this design. The inclusion of stiffeners contributes to mass reduction, and the optimized support structure allows for some cost savings. However, to fully validate the proposed solutions, multiple real-world test prints are necessary.

A draft of the design is presented in Figure 11, illustrating key dimensions. It is important to note that the pores depicted in the porous core are not intended to represent the final pore structure. While the pore radius corresponds to the calculations from the sponge sizing section, various lattice structures should be explored. The representation of the porous core includes a selected number of pore circles for visualization purposes.

It is worth noting that the tank does not include top or bottom plates. Since only the cross-section was designed using the ASME code method, the end plates are assumed to have the same thickness as the walls and are intended to cover the top and bottom portion of the tank. These plates can be welded on using EB-welding, as has been done in previous similar projects [12]. This approach also ensures compliance with requirement PAMGM-STK-02-SYS-07-AM-08, which prohibits the creation of entirely monolithic structures, and requirement PAMGM-STK-02-SYS-05-AM-02, which prevents the formation of hollow cavities. Additionally, manufacturing the main walls, sponge, and top and bottom plates separately reduces potential material loss due to print failures.

Table 12: Overview of final chosen design

Property | Value
Material | Ti6Al4V
Structure Type | 5 Stiffeners
Propellant | AF-M315E
Wall Thickness (mm) | 1.18
Rdown (mm) | 0.750
Rup (mm) | 0.840

Vvane (m³
) | 3.41e-07
Vane Mass (kg) | 1.51e-03
rsponge (mm) | 4.21
Rsponge (mm) | 22.8
hsponge (mm) | 90.0
tsponge (mm) | 0.180
Nsponge | 10

Vsponge (m³
) | 4.01e-05
rlattice (mm) | 0.550
Sponge Mass (kg) | 0.177
Support Mass (kg) | 0.0163
Support Cost (€) | 6.86
Total Mass (kg) | 0.431
Total Cost (€) | 188

## Conclusion

In conclusion, this report aimed to answer two key research questions:

RQ1: What is the most suitable design for a parallelepiped-shaped tank to meet the identified constraints and requirements?
The report concluded that an externally stiffened, ribbed structure with a uniform wall thickness is the optimal solution. This design strikes a balance between a non-stiffened, uniform-thickness structure and a more complex internal lattice structure. Additionally, the ribs offer the advantage of serving as mounting points for the surrounding structure.

RQ2: What are the most suitable materials, dimensions, and shape/fluidic interfaces to enable a fully operational tank design?
It was determined that Titanium, specifically Ti-6Al-4V, is the most suitable material for this application. Despite its higher cost, Titanium’s excellent mechanical properties and compatibility with green monopropellants and additive manufacturing make it ideal for the task. Regarding fluidic interfaces, surface tension devices provide a simple yet effective method for guiding and storing propellant. This approach has been deemed sufficient for the types of missions this tank is designed for.

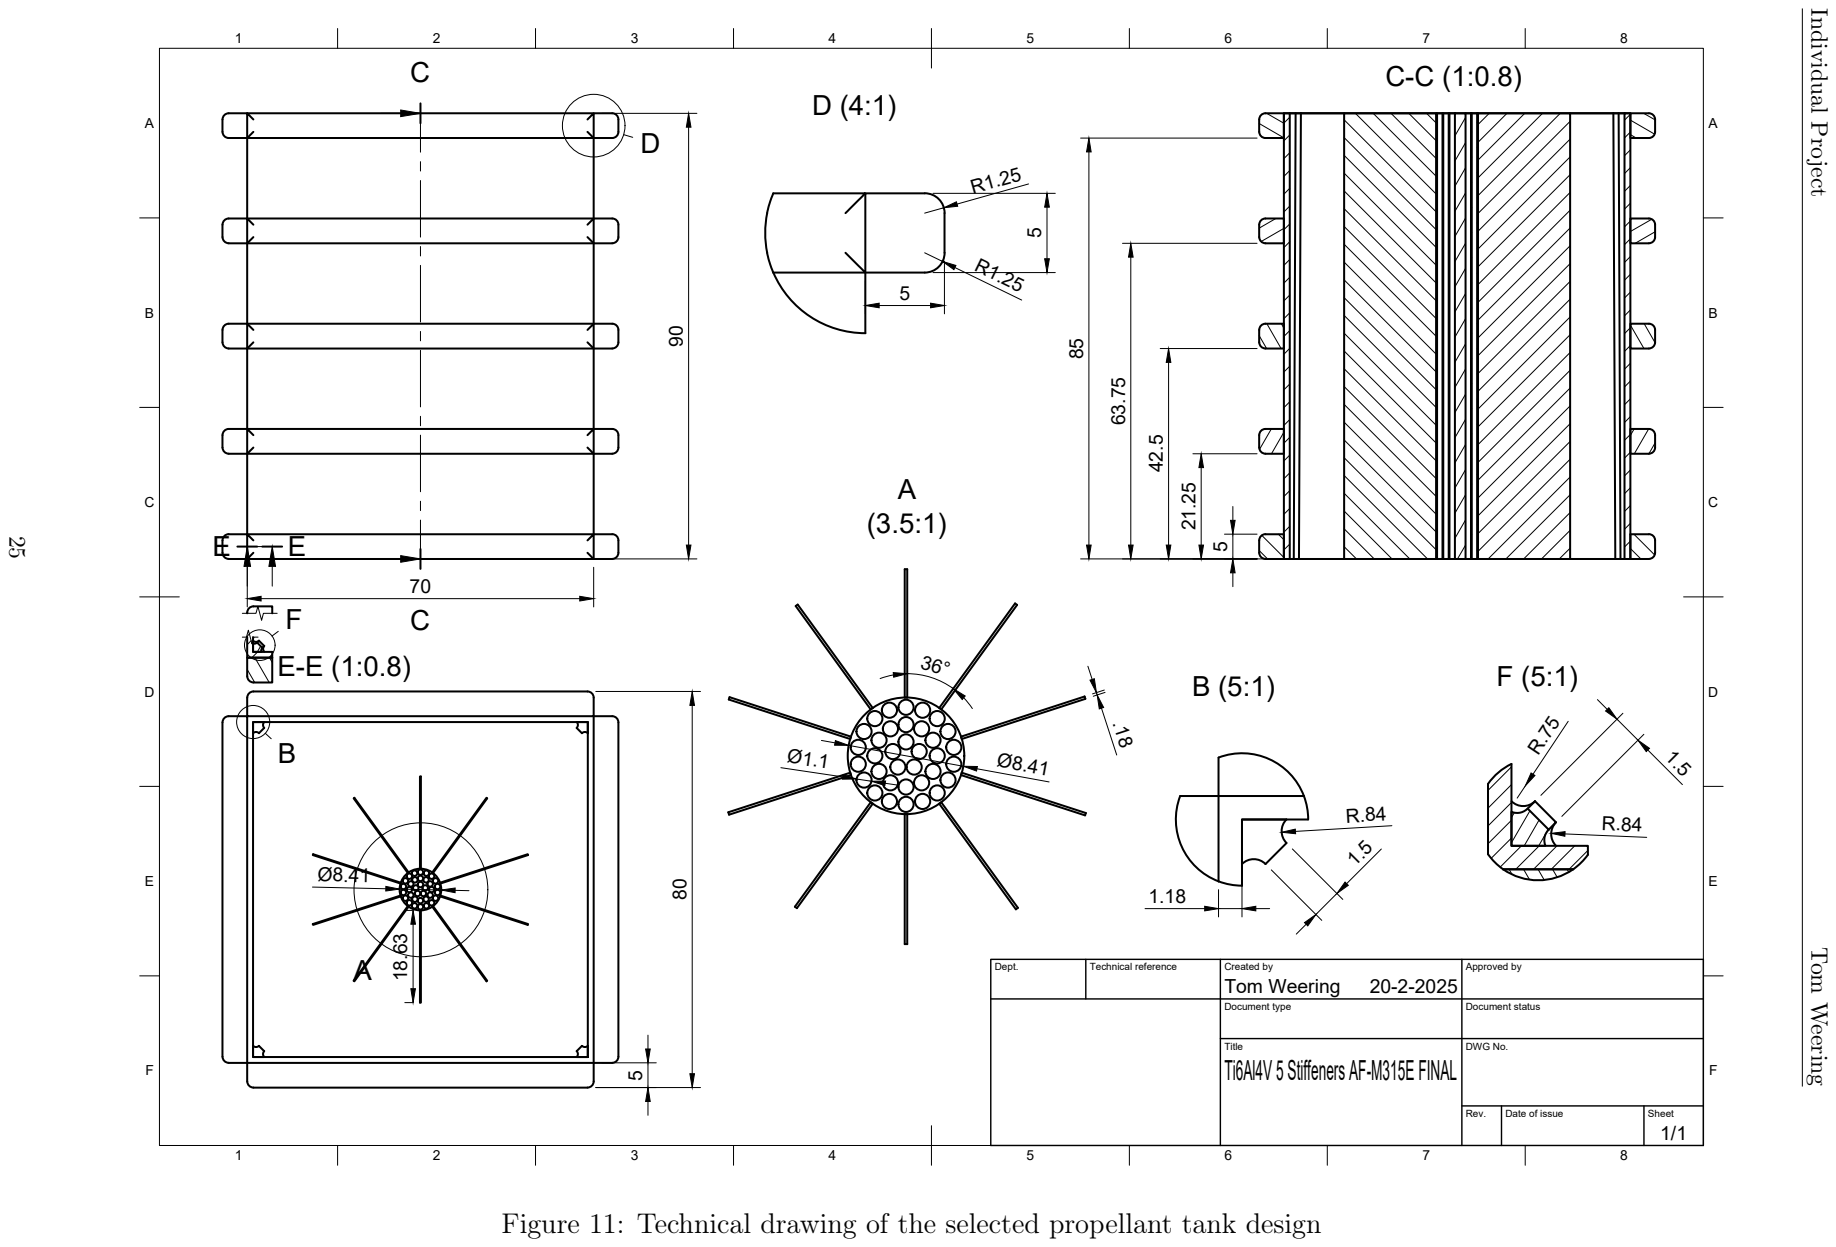
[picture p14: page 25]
Dept.; Technical reference; Created by; Approved by; Document type; Document status; Title; DWG No.; Rev.; Date of issue; Sheet

Individual Project Tom Weering

Tom Weering ⁹⁰

Ti6Al4V 5 Stiffeners AF-M315E FINAL

Figure 11: Technical drawing of the selected propellant tank design

## References

[1] Hassan Mohamed Abdelalim Abdalla, Daniele Casagrande, Francesco De Bona, Thomas De Monte, Marco Sortino, and Giovanni Totis. An optimized pressure vessel obtained by metal additive manufacturing: Preliminary results. International Journal of Pressure Vessels and Piping, 192:104434, 2021.
[2] American Society of Mechanical Engineers. | ASME BPVC 2021 Section II
Part D (Metric). | ASME Boiler and Pressure Vessel Code, 2021. | Avail-
able at: | https://dl.gasplus.ir/standard-ha/Standard-ASME/ASME%20BPVC%
202021%20Section%20II%20part%20D%20(metric).pdf. (https://dl.gasplus.ir/standard-ha/Standard-ASME/ASME%20BPVC%202021%20Section%20II%20part%20D%20(metric).pdf)
[3] ASME Boiler and Pressure Vessel Committee. 2017 ASME Boiler & Pressure Vessel Code: Rules for Construction of Pressure Vessels, Division 1. American Society of Mechanical Engineers (ASME), New York, NY, USA, 2017 edition, July 2017.
[4] A. E. Blach, V. S. Hoa, C. K. Kwok, and A. K. W. Ahmed. Rectangular pressure vessels of finite length. ASME Journal of Pressure Vessel Technology, 1990. Accessed on 02/18/2017.
[5] Daniel Cavender. Emerging Low Toxicity “Green” Chemical Propulsion Technologies for SmallSats. NASA Technical Reports Server, September 2020.
[6] A. Cervone. Micro-Propulsion. Faculty of Aerospace Engineering, Delft University of Technology, v4.0 edition, June 2022. Lecture Notes AE4S07.
[7] Colibrium Additive. | Eb-pbf printers. | https://www.colibriumadditive.com/
printers/eb-pbf-printers, (https://www.colibriumadditive.com/printers/eb-pbf-printers) 2025. Accessed: 2025-02-20.
[8] Jr. D. E. Jaekle. Propellant management device conceptual design and analysis: Vanes. In 27th AIAA/SAE/ASME/ASEE Joint Propulsion Conference, number AIAA-91-2172, Sacramento, CA, June 1991. American Institute of Aeronautics and Astronautics (AIAA), AIAA.
[9] Jr. D. E. Jaekle. Propellant management device conceptual design and analysis: Sponges. In Proceedings of the 29th Joint Propulsion Conference and Exhibit, number AIAA-93-1970, Monterey, CA, June 28-30 1993. AIAA/SAE/ASME/ASEE. PMD Technology, Andover, MA.
[10] National Center for Biotechnology Information. Pubchem, 2025. Accessed: 2025-02-25.
[11] Jason W. Hartwig. A detailed historical review of propellant management devices for low gravity propellant acquisition. Technical report, NASA Glenn Research Center, Cleveland, OH, USA, 2023.
[12] G. Huggins, A. Talaksi, E. G. Lightsey, D. Andrews, D. Cavender, C. Diaz, D. Mc-Queen, H. Williams, J. Baker, and M. Kowalkowski. Development of a cubesat-scale green monopropellant propulsion system for nasa’s lunar flashlight mission. In Space Propulsion 2022, pages 9–13, Estoril, Portugal, May 2022. Georgia Institute of Technology, Atlanta, Georgia, 30313; Marshall Space Flight Center, Huntsville, Alabama, 35811; Jet Propulsion Laboratory, California Institute of Technology.

[13] Makerverse. The laser powder bed fusion (l-pbf) design guide, 2025. Accessed: 2025-02-10.
[14] A. E. S. Nosseir, A. Pasini, S. Igarashi, Y. Matsuura, and A. Cervone. Cubesat green propellants am tanks: Efficient designs, propellant management, and chemical compatibility. In Space Propulsion 2022, pages 9–13, Estoril, Portugal, May 2022. Universita di Pisa (UniPi), DICI - Sede di Aerospaziale, Pisa, Italy; HI Aerospace Co., Ltd., 900 Fujiki, Tomioka-shi, Gunma, 370-2398, Japan; Delft University of Technology (TU Delft), Faculty of AE dpt. Space Engineering, Delft, The Netherlands.
[15] Ahmed E. S. Nosseir, Angelo Cervone, and Angelo Pasini. Modular impulsive green monopropellant propulsion system (mimps-g): For cubesats in leo and to the moon. Aerospace, 8(6):169, 2021.
[16] Georgy A. Shcheglov and Alexey V. Mordovskii. Design optimization of cubic-shaped pressurant tank for cubesat propulsion system. Acta Astronautica, 2024.
[17] Ronald A. Spores, Robert Masse, Scott Kimbrel, and Chris McLean. GPIM AF-M315E Propulsion System. In 50th AIAA/ASME/SAE/ASEE Joint Propulsion Conference & Exhibit, Cleveland, Ohio, July 2014. American Institute of Aeronautics and Astronautics.
[18] A. Steckel. Integrated propellant storage and feed system: Fy18 engineering research technical investment program. Technical Report TIP-89, Lincoln Laboratory, Massachusetts Institute of Technology, Lexington, Massachusetts, May 2019.
[19] PMD Technology. Pmd technology: Propellant management devices (pmds), n.d. Accessed: 2025-02-21.
[20] V. Tepponen, S. Westman, P. Nyamekye, and I. Poutiainen. Optimized inconel 718 pressure vessel manufactured with laser powder bed fusion. In 19th Nordic Laser Materials Processing Conference (NOLAMP-2023), volume 1296, page 012019. IOP Publishing, 2023. Corresponding author: vesa.tepponen@lut.fi.
[21] The CubeSat Program, Cal Poly SLO. Cubesat design specification (cds) rev. 13. Technical report, The CubeSat Program, California Polytechnic State University, San Luis Obispo, 2023. Public Domain.
[22] Wikipedia Contributors. SBUDNIC. https://en.wikipedia.org/wiki/SBUDNIC, 2023. Accessed: 2025-02-19.
[23] Ziheng Wu, Sneha Prabha Narra, and Anthony Rollett. Exploring the fabrication limits of thin-wall structures in a laser powder bed fusion process. The International Journal of Advanced Manufacturing Technology, 110:191–207, August 2020. Received: 26 March 2020 / Accepted: 23 July 2020 / Published online: 11 August 2020.

### Code

The full code base can be found at [github]. (https://github.com/tomweering/AE4S07)

main.py

1 | import sys
2 | import os
3 | import toml
4 | import math
5 | import copy
6 | import csv
7 | import numpy as np
8 | import matplotlib . pyplot as plt
9 | import matplotlib . cm as cm
10 | from scipy . interpolate import griddata
11 | from ASME . _Appendix13_7_a import Appendix13_7_aParams ,
Appendix13_7_aCalcs
12 | from ASME . _Appendix13_8_e import _Appendix13_8_eCalcs
13 | from ASME . _Appendix13_7_c import Appendix13_7_cParams ,
Appendix13_7_cCalcs
14 from curve import optimize_stiffener_curve

15

16
17 | def read_material_data ( filename ) :
18 | try :
19 | with open ( filename , "r") as file :
20 | return toml . load ( file )
21 | except FileNotFoundError :
22 | print (" TOML file not found .")
23 | return {}

24

25
26 | def calculate_thermal_equilibrium ( material_properties ) :
27 | SOLAR_CONSTANT = 1361 | # W/m^2
28 | BOLTZMANN_CONSTANT = 5.670374419 e -8 | # W/m ^2/ K^4
29 | AREA = 0.1 * 0.1 | # m^2 for a 10 cm x 10 cm plate

30
31 | absorptivity = material_properties [" absorptivity "]
32 | emissivity = material_properties [" emissivity "]

33
34 | left_side = absorptivity * AREA * SOLAR_CONSTANT
35 | right_side_factor = emissivity * BOLTZMANN_CONSTANT * AREA

36
37 | temperature_kelvin = ( left_side / right_side_factor ) ** 0.25
38 | return temperature_kelvin

39

40
41 def interpolate_allowable_stress ( material_properties , temperature_celsius ) :
42 | room_temp_stress = material_properties . get ("
allowable_stress_mpa_room_temp ", 0)
43 | elevated_temp_stress = material_properties . get ("
allowable_stress_mpa_300C ", 0)

44
45 | if temperature_celsius <= 20:
46 | return room_temp_stress
47 | elif temperature_celsius >= 300:

48 | return elevated_temp_stress

49
50 | interpolated_stress = room_temp_stress + ( temperature_celsius - 20)
* (
51 | ( elevated_temp_stress - room_temp_stress ) / (300 - 20)
52 | )
53 | return interpolated_stress

54

55
56 | def run_pressure_vessel_analysis ( material_properties , allowable_stress ) :
57 | thickness_range = np . linspace (0.1 , 7.5 , 500) / 1000 | # Thickness
values in meters
58 | pressure_range = np . linspace (0.01 , 2 , 100) * 10**6 | # Pressure
values in Pa

59
60 | points = []
61 | labels = []

62
63 | for thickness in thickness_range :
64 | for pressure in pressure_range :
65 | params_inner = Appendix13_7_aParams (
66 | long_side_length_inside =(70 / 1000) ,
67 | short_side_length_inside =(70 / 1000) ,
68 | internal_pressure = pressure ,
69 | short_side_thickness = thickness ,
70 | long_side_thickness = thickness ,
71 | allowable_stress = allowable_stress ,
72 | joint_efficiency =1 ,
73 | )

74
75 | params_outer = copy . deepcopy ( params_inner )
76 | params_outer . evalAtOuterWalls = True

77
78 | calc_inner = Appendix13_7_aCalcs ( params_inner )
79 | calc_outer = Appendix13_7_aCalcs ( params_outer )

80
81 | max_inner_stress = max (
82 | abs ( calc_inner . S_T_N () ) , abs ( calc_inner . S_T_Q_short () ) ,
abs ( calc_inner . S_T_M () ) , abs ( calc_inner . S_T_Q_long () )
83 | )
84 | max_outer_stress = max (
85 | abs ( calc_outer . S_T_N () ) , abs ( calc_outer . S_T_Q_short () ) ,
abs ( calc_outer . S_T_M () ) , abs ( calc_outer . S_T_Q_long () )
86 | )

87
88 | stress_limit = 1.5 * allowable_stress

89
90 | is_safe = max_inner_stress <= stress_limit and
max_outer_stress <= stress_limit

91
92 | points . append (( thickness * 1000 , pressure / 10**6) ) | #
Convert thickness to mm , pressure to MPa
93 | labels . append ( is_safe )

94
95 | return points , labels

96
97 def run_rounded_structure_analysis ( material_properties , allowable_stress ) :

98 | thickness_range = np . linspace (0.1 , 7.5 , 500) / 1000 | # Thickness
values in meters
99 | pressure_range = np . linspace (0.01 , 2 , 100) * 10**6 | # Pressure
values in Pa

100
101 | points = []
102 | labels = []

103
104 | for thickness in thickness_range :
105 | for pressure in pressure_range :
106 | # Define input parameters for Appendix 13 -7(c) analysis
107 | params_inner = Appendix13_7_cParams (
108 | internal_pressure = pressure ,
109 | corner_radius = 100 / 1000 , | # 15 mm in meters
110 | short_side_half_length =70 / 2 / 1000 , | # 35 mm as half
length in meters
111 | long_side_half_length =70 / 2 / 1000 , | # 35 mm as half
length in meters
112 | thickness = thickness
113 | )

114
115 | calc_inner = Appendix13_7_cCalcs ( params_inner )

116
117 | # Evaluate at outer walls
118 | params_outer = copy . deepcopy ( params_inner )
119 | params_outer . eval_at_outer_walls = True
120 | calc_outer = Appendix13_7_cCalcs ( params_outer )

121
122 | # Maximum stress evaluations
123 | max_inner_stress = max (
124 | abs ( calc_inner . S_T_C () ) , abs ( calc_inner . S_T_D () ) , abs (
calc_inner . S_T_A () ) , abs ( calc_inner . S_T_B () )
125 | )
126 | max_outer_stress = max (
127 | abs ( calc_outer . S_T_C () ) , abs ( calc_outer . S_T_D () ) , abs (
calc_outer . S_T_A () ) , abs ( calc_outer . S_T_B () )
128 | )

129
130 | stress_limit = 1.5 * allowable_stress

131
132 | is_safe = max_inner_stress <= stress_limit and
max_outer_stress <= stress_limit

133
134 | points . append (( thickness * 1000 , pressure / 10**6) ) | #
Convert thickness to mm , pressure to MPa
135 | labels . append ( is_safe )

136
137 | return points , labels

138

139
140 def run_stiffened_structure_analysis ( material_properties , allowable_stress , n_stiffeners ) :
141 | thickness_range = np . linspace (0.1 , 7.5 , 500) / 1000 | # Thickness
values in meters
142 | pressure_range = np . linspace (0.01 , 2 , 100) * 10**6 | # Pressure
values in Pa

143
144 | points = []

145 | labels = []

146
147 | side_length = 70 / 1000
148 | stiffner_thickness = 5 / 1000
149 | stiffner_height = 5 / 1000
150 | total_height = 90 / 1000
151 | # n_stiffeners = 5

152
153 | pitch = ( total_height - stiffner_height ) / ( n_stiffeners - 1)

154
155 | for thickness in thickness_range :
156 | for pressure in pressure_range :
157 | params = {
158 | "P": pressure ,
159 | "H": 0.07 ,
160 | "h": 0.07 ,
161 | "t_1 ": thickness ,
162 | "t_2 ": thickness ,
163 | " ts_1 ": stiffner_thickness ,
164 | " ts_2 ": stiffner_thickness ,
165 | "A_1 ": 0.07 * stiffner_thickness ,
166 | "A_2 ": 0.07 * stiffner_thickness ,
167 | "H_1 ": stiffner_height ,
168 | "h_1 ": stiffner_height ,
169 | "p": pitch ,
170 | "S": allowable_stress ,
171 | "S_y ": material_properties . get (" yield_strength_mpa ", 0)
*10**6 ,
172 | "E_2 ": material_properties . get ("
| modulus_of_elasticity_gpa ", 0) *10**9 ,
173 | "E_3 ": material_properties . get ("
| modulus_of_elasticity_gpa ", 0) *10**9 ,
174 | }

175
176 | params_obj = type (" Params ", ( object ,) , params ) ()
177 | calc = _Appendix13_8_eCalcs ( params_obj )

178
179 | max_stress = max(
180 | abs ( calc . S_T_N () ) , abs ( calc . S_T_Q_short () ) , abs ( calc .
| S_T_M () ) , abs ( calc . S_T_Q_long () )
181 | )

182
183 | stress_limit = 1.5 * allowable_stress

184
185 | is_safe = max_stress <= stress_limit

186
187 | points . append (( thickness * 1000 , pressure / 10**6) ) | #
| Convert thickness to mm , pressure to MPa
188 | labels . append ( is_safe )

189
190 | return points , labels

191

192

193
194 | def plot_pressure_thickness_analysis ( materials_data ) :
195 | # Ask the user which structure type to plot
196 | structure_type = input (" Enter ’ unstiffened ’ to plot the unstiffened
structure , ’stiffened ’ to plot the stiffened structure , or ’rounded ’

to plot the rounded structure : "). strip () . lower ()

197
198 | # Create the figures directory if it doesn ’t exist
199 | figures_dir = os . path . join ( os . path . dirname ( os . path . abspath ( __file__ )
) , " figures ")
200 | if not os . path . exists ( figures_dir ) :
201 | os . makedirs ( figures_dir )

202
203 | fig , axes = plt . subplots (2 , 2 , figsize =(14 , 10) )
204 | plt . subplots_adjust ( hspace =0.4 , wspace =0.4)

205
206 | for ax , ( material_name , material_properties ) in zip ( axes . ravel () ,
| materials_data . items () ) :
207 | thermal_equilibrium_temp = calculate_thermal_equilibrium (
| material_properties )
208 | allowable_stress = interpolate_allowable_stress (
| material_properties , thermal_equilibrium_temp )
209 | allowable_stress = allowable_stress * 10**6 | # Convert to Pa

210
211 | if structure_type == ’stiffened ’:
212 | points , labels = run_stiffened_structure_analysis (
material_properties , allowable_stress , n_stiffeners =5)
213 | elif structure_type == ’rounded ’:
214 | points , labels = run_rounded_structure_analysis (
| material_properties , allowable_stress )
215 | else :
216 | points , labels = run_pressure_vessel_analysis (
| material_properties , allowable_stress )

217
218 | points = np . array ( points )
219 | labels = np . array ( labels )

220
221 | # Prepare grid for contour plot
222 | thickness = points [: , 0]
223 | pressure = points [: , 1]
224 | safe_zone = labels . astype (int )

225
226 | grid_thickness , grid_pressure = np . meshgrid (
227 | np . linspace ( thickness . min () , thickness . max () , 200) ,
228 | np . linspace ( pressure . min () , pressure . max () , 200)
229 | )

230
231 | grid_points = np . column_stack (( grid_thickness . ravel () ,
| grid_pressure . ravel () ) )
232 | interpolated_labels = griddata ( points , safe_zone , grid_points ,
| method =" linear ")

233
234 | # Plot hatched regions
235 | ax . contourf (
236 | grid_thickness , grid_pressure , interpolated_labels . reshape (
| grid_thickness . shape ) ,
237 | levels =[0 , 0.5 , 1] , colors =[" red ", " green "] , alpha =0.3
238 | )

239
240 | ax . set_title ( f" Material : { material_name }")
241 | ax . set_xlabel (" Thickness (mm)")
242 | ax . set_ylabel (" Pressure ( MPa )")
243 | ax . set_xlim ( thickness .min () , thickness . max () )

244 | ax . set_ylim ( pressure .min () , pressure . max () )
245 | ax . grid ( True )

246
247 | plt . suptitle ( f"{ structure_type } Pressure Vessel Safety Analysis for
Different Materials ")

248
249 | # Save the plot to the figures directory
250 | plot_path = os . path . join ( figures_dir , f" pressure_thickness_analysis_
{ structure_type }. png")
251 | plt . savefig ( plot_path )
252 | plt . show ()

253

254
255 | def extract_feasible_solution ( points , labels , target_pressure =2) :
256 | """
257 | Extract the first feasible solution for a pressure near 2 MPa
258 | """
259 | for idx , point in enumerate ( points ) :
260 | pressure = point [1] | # Pressure in MPa
261 | if abs ( pressure - target_pressure ) < 0.1 and labels [ idx ]: | #
Check near 2 MPa and safe design
262 | return point [0] | # Return thickness (mm)
263 | return None

264

265
266 | def calculate_mass_cost ( material_properties , thickness , n_stiffeners ) :
267 | """
268 | Calculate mass and cost of the design based on thickness and number
of stiffeners
269 | """
270 | side_length = 70 / 1000
271 | height = 90 / 1000
272 | stiffener_thickness = 5 / 1000
273 | stiffener_height = 5 / 1000
274 | design_volume = (2 * side_length * thickness + ( side_length - 2 *
thickness ) * thickness ) * height

275
276 | if n_stiffeners > 0:
277 | stiffener_volume = 4 * n_stiffeners * side_length *
stiffener_thickness * stiffener_height
278 | design_volume += stiffener_volume

279
280 | density = material_properties . get (" density_kg_m3 ", 0)
281 | price_per_kg = material_properties . get (" price_per_kg_eur ", 0)

282
283 | mass = design_volume * density
284 | cost = mass * price_per_kg

285
286 | return mass , cost

287

288
289 | def plot_mass_vs_cost ( materials_data ) :
290 | """
291 | Plot mass vs. cost for different materials and stiffener
configurations
292 | """
293 | fig , ax = plt . subplots ( figsize =(10 , 6) )

294

295 | markers = {
296 | " Unstiffened ": "o",
297 | "2 Stiffeners ": "s",
298 | "3 Stiffeners ": "^",
299 | "4 Stiffeners ": "v",
300 | "5 Stiffeners ": "D"
301 | }

302
303 | all_points = []
304 | material_colors = {}
305 | color_map = cm . get_cmap (’tab10 ’, len ( materials_data ) )

306
307 | for idx , ( material_name , material_properties ) in enumerate (
| materials_data . items () ) :
308 | thermal_equilibrium_temp = calculate_thermal_equilibrium (
| material_properties )
309 | allowable_stress = interpolate_allowable_stress (
| material_properties , thermal_equilibrium_temp )
310 | allowable_stress *= 10 ** 6

311
312 | masses = []
313 | costs = []
314 | labels = []

315
316 | # Unstiffened structure
317 | points , safe_labels = run_pressure_vessel_analysis (
| material_properties , allowable_stress )
318 | points = np . array ( points )
319 | safe_labels = np . array ( safe_labels )

320
321 | thickness = extract_feasible_solution ( points , safe_labels )
322 | if thickness :
323 | thickness_m = thickness / 1000
324 | mass , cost = calculate_mass_cost ( material_properties ,
| thickness_m , n_stiffeners =0)
325 | masses . append ( mass )
326 | costs . append ( cost )
327 | labels . append (" Unstiffened ")
328 | all_points . append (( mass , cost , material_name , " Unstiffened ",
| thickness ) )

329
330 | # Stiffened structures
331 | for n_stiffeners in range (2 , 6) :
332 | points , safe_labels = run_stiffened_structure_analysis (
| material_properties , allowable_stress , n_stiffeners )
333 | points = np . array ( points )
334 | safe_labels = np . array ( safe_labels )

335
336 | thickness = extract_feasible_solution ( points , safe_labels )
337 | if thickness :
338 | thickness_m = thickness / 1000
339 | mass , cost = calculate_mass_cost ( material_properties ,
| thickness_m , n_stiffeners = n_stiffeners )
340 | masses . append ( mass )
341 | costs . append ( cost )
342 | labels . append ( f"{ n_stiffeners } Stiffeners ")
343 | all_points . append (( mass , cost , material_name , f"{
| n_stiffeners } Stiffeners ", thickness ) )

344
345 | # Assign color to the material
346 | material_colors [ material_name ] = color_map ( idx )

347
348 | # Plot mass vs. cost for each material
349 | for i , label in enumerate ( labels ) :
350 | ax . scatter ( costs [ i ] , masses [ i ] , color = material_colors [
material_name ] , marker = markers [ label ])
351 | #ax. annotate (label , ( costs [i] , masses [i]))

352
353 | # Calculate distances from the origin and print the top 10 closest
points
354 | distances = [(( mass **2 + cost **2) **0.5 , mass , cost , material_name ,
structure_type , thickness ) for mass , cost , material_name , structure_type , thickness in all_points ]
355 | distances . sort ()
356 | print ("Top 20 closest points to the origin (0 ,0):")
357 | for i in range (20) :
358 | distance , mass , cost , material_name , structure_type , thickness =
| distances [ i]
359 | print ( f" Material : { material_name } , Structure : { structure_type } ,
Mass : { mass :.2 f} kg , Cost : { cost :.2 f} | , Thickness : { thickness :.2 f}
| mm")

360
361 | ax . set_title (" Mass vs Cost for Different Structures and Materials ")
362 | ax . set_xlabel (" Cost ( | )")
363 | ax . set_ylabel (" Mass (kg)")
364 | ax . grid ( True )

365
366 | # Create custom legend
367 | handles = [ plt . Line2D ([0] , [0] , marker = markers [ label ] , color =’w’,
label = label , markerfacecolor =’k’, markersize =10) for label in markers ]
368 | handles += [ plt . Line2D ([0] , [0] , marker =’o’, color =’w’, label =
material_name , markerfacecolor = color , markersize =10) for material_name , color in material_colors . items () ]
369 | ax . legend ( handles = handles , title =" Legend ")

370
371 | # Save and show plot
372 | plot_path = os . path . join (" figures ", " mass_cost_tradeoff . png ")
373 | plt . savefig ( plot_path )
374 | plt . show ()

375
376 | # Save designs to CSV
377 | csv_path = os . path . join (" data ", " designs . csv ")
378 | with open ( csv_path , mode =’w’, newline =’’) as file :
379 | writer = csv . writer ( file )
380 | writer . writerow ([" Material ", " Structure Type ", " Mass (kg)", "
Cost ( | )", " Thickness (mm)"])
381 | for mass , cost , material_name , structure_type , thickness in
| all_points :
382 | writer . writerow ([ material_name , structure_type , mass , cost ,
| thickness ])

383

384

385
386 def capillary_length ( material_properties , thickness ) :

387 | surface_tension = material_properties . get (" surface_tension_mN_per_m "
, 0)
388 | density = material_properties . get (" density_g_per_cm3 ", 0)
389 | # convert to SI units
390 | surface_tension = surface_tension * 10** -3
391 | density = density * 10**3

392
393 | # assumption on acceleration on 3U cubesat
394 | m_assumed = 5.5 #[kg]
395 | T_assumed = 1.0 #[N]
396 | a = T_assumed / m_assumed #[m/s ^2]

397
398 | # calculate capillary length
399 | lamda = ( surface_tension / ( density * a ) ) **(1/2)

400
401 | # get fillet radius to resist capillary effect
402 | L = math . sqrt ((35 - thickness ) **2 + (35 - thickness ) **2)
403 | R = L - math . sqrt (( lamda **2) /4)

404
405 | return lamda , R

406
407 # TODO make function that compares PMD ( Propellant Management Device ) designs
408 | # fillet on the edges to resist the capillary effect
409 | # vanes to transfer fluid from the corners to the center
410 | # sponge to absorb the fluid

411
412 # for the vane get surface area from frustum (1/4) lateral area (1/2 for total )
413 # source : https :// www . calculatorsoup . com / calculators / geometry - solids / conicalfrustum .php

414
415 | def vane_sizing ( material_properties ) :
416 | flow_rate = 30 #[mL / min] ( from MiMPS -G e- micro pump )
417 | # flow_rate = 420 #[ mL / min ] ( exaggerated )
418 | viscosity = material_properties . get (" absolute_viscosity_mPas ", 0)
419 | density = material_properties . get (" density_g_per_cm3 ", 0)
420 | surface_tension = material_properties . get (" surface_tension_mN_per_m "
, 0)
421 | delta = (1.5/1000) | #[m] thickness of " sheet metal vane " (in
accordance with printable thickness )
422 | L = (90/1000) | #[m] length of the vane

423
424 | # convert to SI units
425 | flow_rate = flow_rate * 10** -6 / 60 | #[m^3 / s]
426 | viscosity = viscosity * 10** -3 | #[Pa s]
427 | density = density * 10**3 | #[kg / m ^3]
428 | surface_tension = surface_tension * 10** -3 | #[N / m]

429
430 | # Slant height of a conical frustum :
431 | #s = | (( r1 - r2)^2 + h^2)
432 | # Lateral surface area of a conical frustum :
433 | # S = | * (r1 + r2) * s = | * (r1 + r2) * | (( r1 - r2)^2 + h ^2)
434 | # Volume of a conical frustum :
435 | #V = (1/3) * | * h * (r1 ^2 + r2 ^2 + (r1 * r2))

436
437 | vanes = []

438

439 | # Get relation for Rdown and Rup from knowing total height and
overhang angle can at most be 45 degrees
440 | for R in np . arange ( delta /2 , 10* delta , 0.001) :
441 | for theta in np . arange (0 , math . pi /4 , 0.001) :
442 | R_down = R
443 | R_up = R + L * math . tan ( theta )

444
445 | s = math . sqrt (( R_up - R_down ) **2 + L **2)
446 | S = math . pi * ( R_up + R_down ) * s
447 | V = (1/3) * math . pi * L * ( R_up **2 + R_down **2 + ( R_up *
R_down ) )
448 | A = S / 2 | #[m ^2] (1/2 of the
TOTAL lateral area )
449 | #Q = flow_rate / 4 | # assume 4 vanes ,
one for each corner
450 | Q = flow_rate

451

452
453 | viscous_losses = (2* viscosity * Q * L ) / A | # assume wetted area
= surface area
454 | dynamic_losses = ( density * Q **2) /(2* A **2)

455
456 | young_laplace = surface_tension * (1/ R_down - 1/ R_up )

457
458 | V_vane = R_up * delta * L + L *( R_up + delta /2) **2 | # assumption on
volume of vane

459
460 | # Print pressures
461 | # print (f" viscous_losses : { viscous_losses } , dynamic_losses : {
dynamic_losses } , young_laplace : { young_laplace }")

462
463 | # Check if absolute value of yound_laplace is greater than
combined absolute value of viscous and dynamic losses
464 | if abs ( young_laplace ) > abs ( viscous_losses + dynamic_losses )
:
465 | vane = [ R_down , R_up , V_vane ]
466 | vanes . append ( vane )

467

468
469 | # Sort vanes based on V_vane and return the smallest one
470 | min_vane = min ( vanes , key = lambda x : x [2])
471 | # print (f" R_down : { min_vane [0]*1000} mm , R_up : { min_vane [1]*1000} mm
")
472 | # print (f" viscous_losses : { viscous_losses } , dynamic_losses : {
dynamic_losses } , young_laplace : { young_laplace }")

473
474 | return min_vane

475
476 | def sponge_sizing ( propellant_properties , thickness ) :
477 | # sigma , rho , a, V_req , r_sponge , t =0.3e -3 , g_min_fab =0.5e -3 ,
g_max_ratio =2
478 | propellant_name = propellant_properties . get (" name ", "")

479
480 | # Obtain propellant properties
481 | sigma = propellant_properties . get (" surface_tension_mN_per_m ", 0) *
10** -3
482 | rho = propellant_properties . get (" density_g_per_cm3 ", 0) * 10**3
483 | # assumption on acceleration on 3U cubesat

484 | m_assumed = 5.5 #[kg]
485 | T_assumed = 1.0 #[N]
486 | a = T_assumed / m_assumed #[m/s ^2]

487
488 | # Get V_req through burntime and flowrate
489 | burntime = 10 #[s] ( estimate )
490 | flowrate = 30 #[mL / min ] ( from MiMPS -G e- micro pump )
491 | V_req = ( flowrate * 10** -6 / 60) * burntime #[m ^3]

492
493 | P_bubble_point = 200 | # Bubble point pressure (Pa) ( assumption )
494 | # ratio = 47438 | # Get thickness through simple cantilever
model s source : https :// apps . dtic . mil / sti / pdfs / AD1098357 . pdf

495
496 | sponges = []

497
498 | # Cycle through a range of radii and thicknesses
499 | for N in range (10 ,36) :
500 | r = (2* sigma ) / P_bubble_point
501 | g_max = math . sqrt ( sigma /( a * rho ) )
502 | R = ( g_max * N ) /(2* math . pi )
503 | h = V_req /( math . pi * r **2)

504
505 | # TODO Add requirement to get thickness by setting constraint on
percentage of total volume dedicated to PMD
506 | V_tank = ((70/1000) -2* thickness ) **2 * (90/1000 - 2* thickness )
507 | V_PMD = 0.1 * V_tank
508 | t = V_PMD / ( N *( R - r ) )

509
510 | if h > 90 e -3:
511 | h = 90 e -3
512 | r = math . sqrt (( V_req ) /( h * math . pi ) )
513 | r_lattice = (2* sigma ) / P_bubble_point

514

515
516 | if R < 0.05:
517 | sponge = [ propellant_name , r , R , h , t , N , V_PMD , r_lattice ]
518 | sponges . append ( sponge )

519
520 | # Sort sponges based on V and return the smallest one
521 | best_design = min ( sponges , key = lambda x : x [5])

522
523 | if best_design [2] >= 90 e -3:
524 | print ("r too large to rely on surface tension or capillary
action to prevent gas injection . Lattice is required .")

525
526 | return best_design

527

528
529 | def PMD_design () :
530 | # Material densities
531 | densities = {" Ti6Al4V ": 4420 , " StainlessSteel316L ": 8000 , "
StainlessSteel304L ": 7930 , " Inconel625 ": 8440}
532 | structure_types = {" Unstiffened ": 0 , "2 Stiffeners ": 2 , "3
Stiffeners ": 3 , "4 Stiffeners ": 4 , "5 Stiffeners ": 5}

533
534 | designs_file_path = os . path . join (" data ", " designs . csv ")
535 | output_file_path = os . path . join (" data ", " PMD_designs . csv ")

536

537 | infill = 0.15 | # assumed for support and non - structural 15% infill

538
539 | with open ( designs_file_path , mode =’r’) as file :
540 | reader = csv . DictReader ( file )
541 | designs = list ( reader )

542
543 | with open ( output_file_path , mode =’w’, newline =’’) as file :
544 | writer = csv . writer ( file )
545 | writer . writerow ([" Material ", " Structure Type ", " Propellant ", "
Thickness (mm)", " R_down (mm)", " R_up (mm)", " V_vane (m ^3) ", " Vane Mass (kg)", " r_sponge (mm)", " R_sponge (mm)", " h_sponge (mm)", " t_sponge (mm)", " N_sponge ", " V_sponge (m ^3) ", " r_lattice (mm)", "
Sponge Mass (kg)", " Support Mass (kg)", " Support Cost ( | )", " Total
Mass (kg)", " Total Cost ( | )"])

546
547 | for design in designs :
548 | material = design [" Material "]
549 | cost = float ( design [" Cost ( | )"])
550 | mass = float ( design [" Mass (kg)"])
551 | price_per_kg = cost / mass
552 | structure_type = design [" Structure Type "]
553 | thickness = float ( design [" Thickness (mm)"]) / 1000 | #
Convert thickness to meters
554 | density_material = densities . get ( material , 0)

555
556 | propellant_data = read_material_data ( os . path . join ( base_dir ,
" data ", " propellants . toml ") )
557 | if propellant_data :
558 | propellants = propellant_data . get (" propellants ", {})
559 | for propellant_name , propellant_properties in
propellants . items () :

560
561 | lamda , R = capillary_length ( propellant_properties ,
thickness )
562 | lamda = lamda / 1000 | # Convert from mm to m
563 | R = R / 1000 | # Convert from mm to m

564
565 | h = 90 / 1000 | # Height in meters

566
567 | # Calculate the volume of the fillet
568 | volume_fillet = 0.5 * R * h

569
570 | # Calculate the mass of the fillet assuming 15%
infill
571 | mass_fillet = volume_fillet * density_material *
infill

572
573 | # Get mass of support for stiffeners
574 | if structure_type == " Unstiffened ":
575 | n_stiffeners = 0
576 | mass_support = 0
577 | else :
578 | n_stiffeners = structure_types . get (
structure_type , 0)
579 | area_support = optimize_stiffener_curve ( L =90 , h
=5 , n = n_stiffeners , t =5 , plot = False ) [1]
580 | volume_support = 4 * ( n_stiffeners - 1) * 70 *
area_support

581 | volume_support = volume_support / 10**9 | #
Convert from mm ^3 to m^3
582 | mass_support = volume_support * density_material
* infill

583
584 | vane_design = vane_sizing ( propellant_properties )
585 | vane_mass = vane_design [2] * density_material

586
587 | sponge_design = sponge_sizing ( propellant_properties ,
thickness )
588 | sponge_mass = sponge_design [6] * density_material

589
590 | total_mass = vane_mass + sponge_mass + mass
591 | support_cost = mass_support * price_per_kg
592 | total_cost = total_mass * price_per_kg +
support_cost

593
594 | # TODO limit the accuracy to 0.00 i.e. 3 significant
figures
595 | writer . writerow ([ material , structure_type ,
propellant_name , thickness * 1000 , vane_design [0] * 1000 , vane_design
[1] * 1000 , vane_design [2] , vane_mass , sponge_design [1] * 1000 , sponge_design [2] * 1000 , sponge_design [3] * 1000 , sponge_design [4] * 1000 , sponge_design [5] , sponge_design [6] , sponge_design [7] * 1000 , sponge_mass , mass_support , support_cost , total_mass , total_cost ])

596
597 | # print (f" Material : { material } , Structure Type : {
structure_type } , Propellant : { propellant_name } , Thickness : { thickness * 1000} mm , R_down : { vane_design [0] * 1000} mm , R_up : { vane_design
[1] * 1000} mm , V_vane : { vane_design [2]} m^3 , Vane Mass : { vane_mass } kg , r_sponge : { sponge_design [1] * 1000} mm , R_sponge : { sponge_design
[2] * 1000} mm , h_sponge : { sponge_design [3] * 1000} mm , t_sponge : { sponge_design [4] * 1000} mm , N_sponge : { sponge_design [5]} , V_sponge : { sponge_design [6]} m^3 , r_lattice : { sponge_design [7] * 1000} mm , Sponge Mass : { sponge_mass } kg , Support Mass : { mass_support } kg ,
Support Cost : { support_cost } | , Total Mass : { total_mass } kg , Total
Cost : { total_cost } | ")

598
599 # Normalize using min -max scaling , with an option to invert values for minimization
600 | def normalize ( values , invert = False ) :
601 | min_val , max_val = min ( values ) , max ( values )
602 | norm_values = [( v - min_val ) / ( max_val - min_val ) if max_val >
min_val else 0 for v in values ]

603
604 | return [1 - v if invert else v for v in norm_values ] | # Invert if we
want to minimize

605
606 | def trade_off () :
607 | # Dictionary of volumetric ISPs (gs/ c m | )
608 | volumetric_specific_impulse_gs_per_cm3 = {
609 | " AF_M315E ": 391 , " LMP_103S ": 312.48 , " HNP225 ": 245 , " FLP_106 ":
344.6
610 | }

611
612 | # Read CSV file
613 | designs_file_path = os . path . join (" data ", " PMD_designs . csv ")
614 | with open ( designs_file_path , mode =’r’) as file :

615 | reader = csv . DictReader ( file )
616 | designs = list ( reader )

617
618 | # Extract values for normalization
619 | mass_values = []
620 | eff_tank_values = []
621 | cost_values = []
622 | r_lattice_values = []
623 | t_sponge_values = []
624 | support_mass_values = []

625
626 | for design in designs :
627 | mass_values . append ( float ( design [" Total Mass (kg)"]) ) | # Want
LESS
628 | cost_values . append ( float ( design [" Total Cost ( | )"]) ) | # Want
LESS
629 | r_lattice_values . append ( float ( design [" r_lattice (mm)"]) ) | # Want
MORE
630 | t_sponge_values . append ( float ( design [" t_sponge (mm)"]) ) | # Want
MORE
631 | support_mass_values . append ( float ( design [" Support Mass (kg)"]) )
| # Want LESS

632
633 | thickness = float ( design [" Thickness (mm)"])
634 | V_vane = float ( design [" V_vane (m ^3) "])
635 | V_sponge = float ( design [" V_sponge (m ^3) "])

636
637 | V_tank_mm3 = (70 - 2* thickness ) ** 2 * (90 - 2* thickness ) | #
m m
638 | V_tank = V_tank_mm3 / 10**9 | # Convert to m
639 | V_propellant = ( V_tank - V_vane - V_sponge ) * (85/90) | # m
640 | V_propellant_cm3 = V_propellant * 10**6 | # Convert to c m
641 | eff_tank_values . append ( V_propellant ) | # Want MORE

642
643 | # Normalize values ( inverting where needed )
644 | mass_norm = normalize ( mass_values , invert = True ) | # LESS is better
645 | eff_tank_norm = normalize ( eff_tank_values ) | # MORE is better
646 | cost_norm = normalize ( cost_values , invert = True ) | # LESS is better
647 | r_lattice_norm = normalize ( r_lattice_values ) | # MORE is better
648 | t_sponge_norm = normalize ( t_sponge_values ) | # MORE is better
649 | support_mass_norm = normalize ( support_mass_values , invert = True ) | #
| LESS is better

650
651 | # Compute printability ( favoring higher r_lattice , t_sponge , and
| lower support mass )
652 | printability_values = [
653 | ( r + t + s ) / 3 for r , t , s in zip ( r_lattice_norm , t_sponge_norm
| , support_mass_norm )
654 | ]

655
656 | # Normalize printability
657 | printability_norm = normalize ( printability_values )

658
659 | # Compute final trade -off score using weights
660 | weights = {" Mass ": 4 , " Effective Tank Volume ": 1 , " Cost ": 3 , "
| Printability ": 2}

661
662 | trade_off_scores = [

663 | ( weights [" Mass "] * m +
664 | weights [" Effective Tank Volume "] * e +
665 | weights [" Cost "] * c +
666 | weights [" Printability "] * p ) / sum ( weights . values () )
667 | for m , e , c , p in zip ( mass_norm , eff_tank_norm , cost_norm ,
| printability_norm )
668 | ]

669
670 | # Store normalized results
671 | for i , design in enumerate ( designs ) :
672 | design [" Normalized Mass "] = mass_norm [ i ]
673 | design [" Normalized Effective Tank Volume "] = eff_tank_norm [ i ]
674 | design [" Normalized Cost "] = cost_norm [ i ]
675 | design [" Normalized Printability "] = printability_norm [ i ]
676 | design ["Trade -off Score "] = trade_off_scores [ i ]

677
678 | # Write updated data with normalized values to a new CSV
679 | output_file_path = os . path . join (" data ", " PMD_designs_with_tradeoff .
| csv ")
680 | with open ( output_file_path , mode =’w’, newline =’’) as file :
681 | fieldnames = designs [0]. keys ()
682 | writer = csv . DictWriter (file , fieldnames = fieldnames )
683 | writer . writeheader ()
684 | writer . writerows ( designs )

685
686 | print ( f"Trade - off analysis completed . Results saved to {
| output_file_path }")

687
688 | # Print top 10 designs with normalized values
689 | designs . sort ( key = lambda x : x ["Trade - off Score "] , reverse = True )
690 | print ("\ nTop 10 designs with Normalized Values :")
691 | for i in range (min (10 , len ( designs ) ) ) :
692 | print ( f"""
693 | Material : { designs [i][ ’ Material ’]}
694 | Structure Type : { designs [i][ ’ Structure Type ’]}
695 | Propellant : { designs [i][ ’ Propellant ’]}
696 | Normalized Mass : { designs [i][ ’ Normalized Mass ’]:.3f}
697 | Normalized Effective Tank Volume : { designs [i][ ’ Normalized
| Effective Tank Volume ’]:.3f}
698 | Normalized Cost : { designs [i][ ’ Normalized Cost ’]:.3f}
699 | Normalized Printability : { designs [i][ ’ Normalized Printability
| ’]:.3f}
700 | Trade -off Score : { designs [i][ ’ Trade - off Score ’]:.3f}
701 | """ )

702
703 | if __name__ == " __main__ ":
704 | base_dir = os . path . dirname ( os . path . abspath ( __file__ ) )
705 | materials_file_path = os . path . join ( base_dir , " data ", " materials . toml
| ")

706
707 | material_data = read_material_data ( materials_file_path )

708
709 | if material_data :
710 | materials = material_data . get (" materials ", {})
711 | # plot_mass_vs_cost ( materials )

712
713 | # plot_pressure_thickness_analysis ( materials )
714 | # plot_stiffened_vs_unstiffened ( materials )

715
716 | PMD_design ()
717 | trade_off ()

Listing 1: Main script

curve.py

1 | import numpy as np
2 | import matplotlib . pyplot as plt
3 | import scipy . integrate as spi

4
5 | def optimize_stiffener_curve (L , h , n , t , plot = True ) :
6 | """
7 | Optimize the stiffener support curve while ensuring the slope does
not exceed 45 degrees .

8
9 | Parameters :
10 | L ( float ): Total height of the box .
11 | h ( float ): Height of stiffener .
12 | n (int ): Number of stiffeners .
13 | t ( float ): Extremity thickness of stiffeners .
14 | plot ( bool ): Whether to generate the plot ( default : True ).

15
16 | Returns :
17 | tuple : (t - y0 , area_above_curve )
18 | """
19 | # Calculate pitch and curve width
20 | P = ( L - h ) / ( n - 1)
21 | curve_width = ( P - h ) / 2 | # Half - width of the curve

22
23 | # Start with initial height guess and reduce if needed
24 | y0 = t

25
26 | # Define x range
27 | x_range = np . linspace (- curve_width , curve_width , 1000)

28
29 | # Adjust y0 until all slopes are | 45 degrees
30 | while True :
31 | # Define the parabolic curve : y = a*x^2 + y0
32 | a = - y0 / curve_width **2 | # Ensuring parabola peaks at (0 , y0)
33 | y_curve = a * x_range **2 + y0

34
35 | # Analytical derivative dy/dx = 2 * a * x
36 | derivative = 2 * a * x_range

37
38 | # Compute angles in degrees
39 | angles = np .abs ( np . arctan ( derivative ) * (180 / np . pi ))

40
41 | # If all angles are <= 45 degrees , break loop
42 | if np .all( angles <= 45) :
43 | break

44
45 | # Reduce y0 slightly if any angle exceeds 45 degrees
46 | y0 -= 0.01

47
48 | # Bounding box area

49 | box_area = 2 * curve_width * y0

50
51 | # Integrate the area under the curve
52 | area_under_curve , _ = spi . quad ( lambda x : a * x **2 + y0 , - curve_width
| , curve_width )

53
54 | # Area above the curve
55 | area_above_curve = box_area - area_under_curve

56

57

58
59 | # Generate plot if requested
60 | if plot :
61 | plt . figure ( figsize =(6 , 4) )
62 | plt . plot ( x_range , y_curve , label = f" Optimized Curve (y0 ={ y0 :.2 f})
| ", color =" blue ")
63 | plt . axhline (0 , color =’gray ’, linestyle =’--’, label =" Stiffener
| Base ")
64 | plt . axvline ( - curve_width , color =’red ’, linestyle =’--’, label ="
| Extremity ")
65 | plt . axvline ( curve_width , color =’red ’, linestyle =’--’)
66 | plt . fill_between ( x_range , y_curve , y0 , color =’lightblue ’, alpha
| =0.5 , label =" Area Above Curve ")
67 | plt . xlabel (" Width (x)")
68 | plt . ylabel (" Height (y)")
69 | plt . legend ()
70 | plt . title (" Optimized Support Curve with Area Calculation ")
71 | plt . grid ()
72 | plt . show ()

73
74 | # Print results
75 | print ( f" Optimized curve height (y0) to keep slope | 45 | : {y0
| :.4 f}")
76 | print ( f" Adjusted thickness (t - y0): {t - y0 :.4 f}")
77 | print ( f" Area above the curve : { area_above_curve :.4 f} [mm ^2] ")

78
79 | return t - y0 , area_above_curve

80
81 | # Example Usage
82 | # adjusted_thickness , area_above = optimize_stiffener_curve (L=90 , h=5 , n
| =2 , t=5 , plot = True )

Listing 2: Optimizes curve for support structure

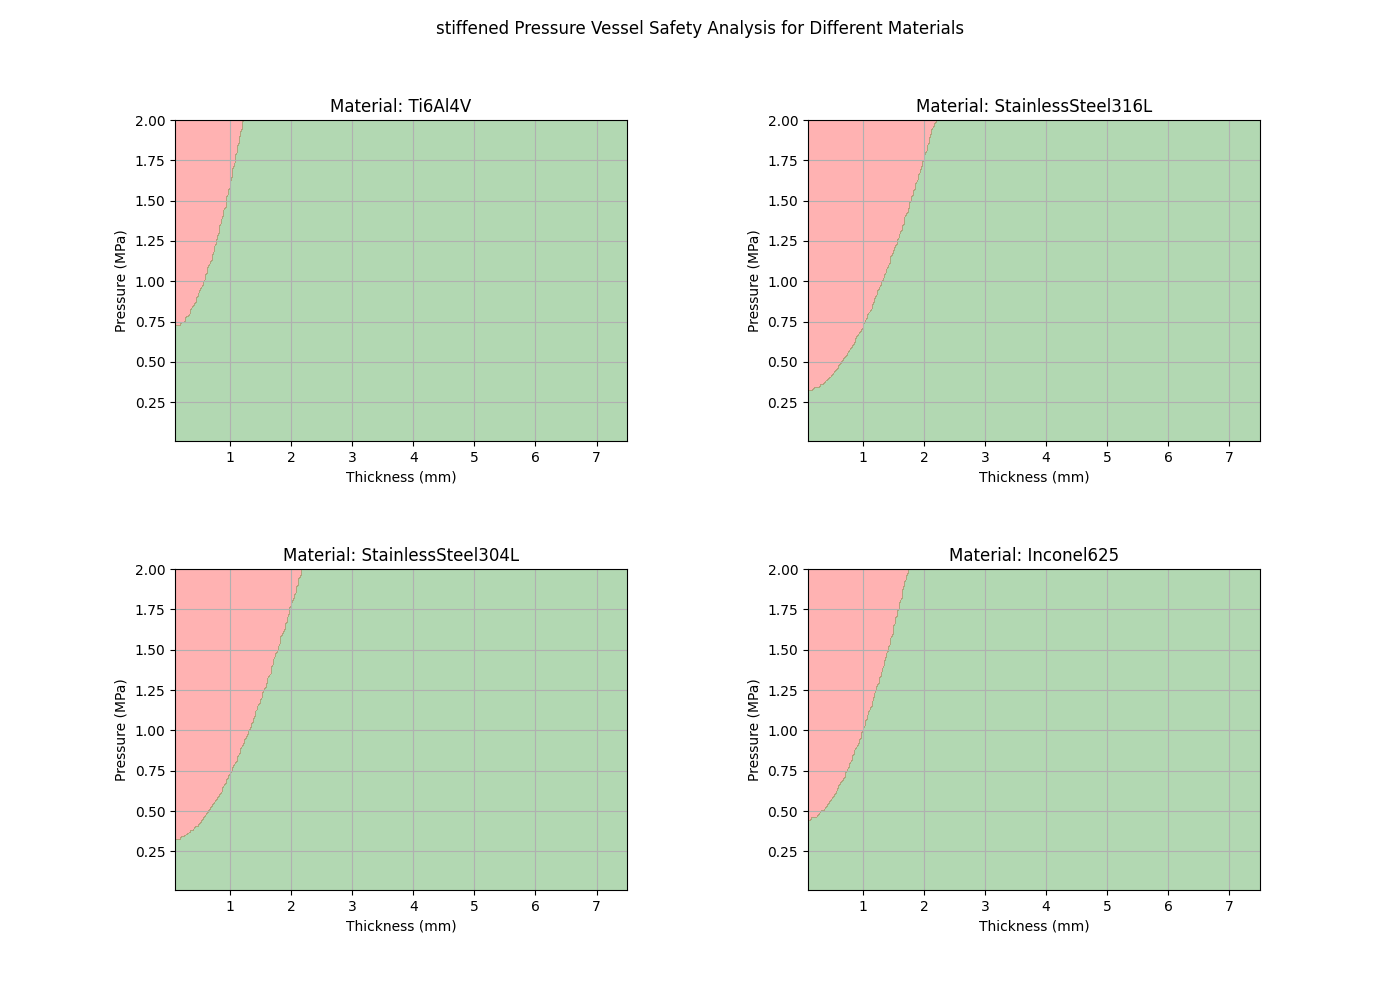
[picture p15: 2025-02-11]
figures/pressure_thickness_analysis_stiffened.png

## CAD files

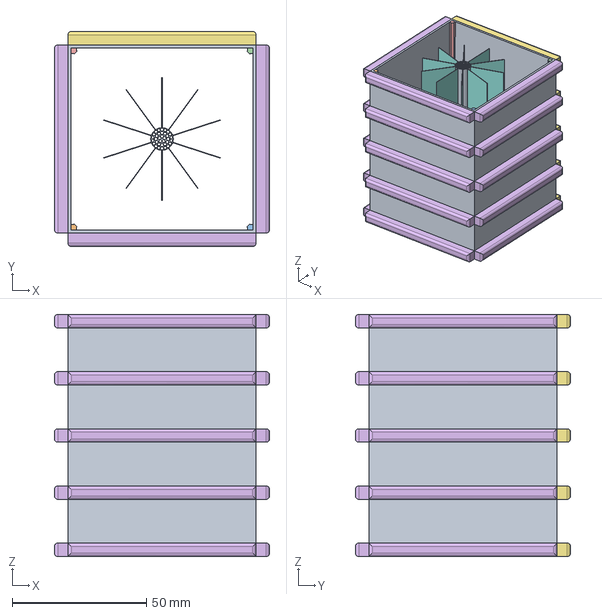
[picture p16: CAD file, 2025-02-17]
models/Ti6Al4V_5_Stiffeners_AF-M315E_v4.step
80.0 x 80.0 x 90.0 mm

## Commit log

2025-02-10 ASME Rectangular Pressure Vessel Analysis
2025-02-11 Added data
    [designs.csv]
2025-02-15 Updated material properties, started with PMD
    [designs.csv]
2025-02-17 Completed trade off
    [PMD_designs.csv, PMD_designs_with_tradeoff.csv]
2025-02-17 Fixed trade-off
    [PMD_designs_with_tradeoff.csv]
2025-02-17 Final selection?
    [PMD_designs_with_tradeoff.csv, Ti6Al4V_5_Stiffeners_AF-M315E_v4.step]
